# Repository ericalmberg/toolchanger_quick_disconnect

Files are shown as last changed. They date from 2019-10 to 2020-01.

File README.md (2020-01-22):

# toolchanger_quick_disconnect

## Statement of Purpose

The PCB in here is intended to be a universal connector board based around the micro-molex 3.0 connectors commonly used in 3D printing electronics. This board in it's current iteration contains 4x 2-pin micro-molex connectors for connections to
- Heater catridge 
- Thermistor
- Part cooling fan
- Hotend fan

The board also includes on 4 pin XH2.54 connector for a stepper motor connection if the tool is direct drive, as well as pinout for 4 additional connections back to the duet for the user's purpose labeled accessory 1-4. These are provided in the form of 0.1" spaced through hole connections. 

The connection back to the duet is provided through a 2-row, 16 pin micro-molex 3.0 connector. The intention is that the toolchanger tool wiring could be replaced with one 16 pin connector, and tools could easily be interchanged to "live" and offline. This still requires a tool library to be built into the duet code in order to store tool pickup location offsets, configurations, z-offsets and any other parameters that need to be changed when switching between tools. 

## Potential Gotchas
 - Watch out for your thermistor/PT100 amplifier inputs. Since these are hardwired at the duet, on the same tool bay the user cannot swap between thermistor based tools and PT100/thermocouple based tools.

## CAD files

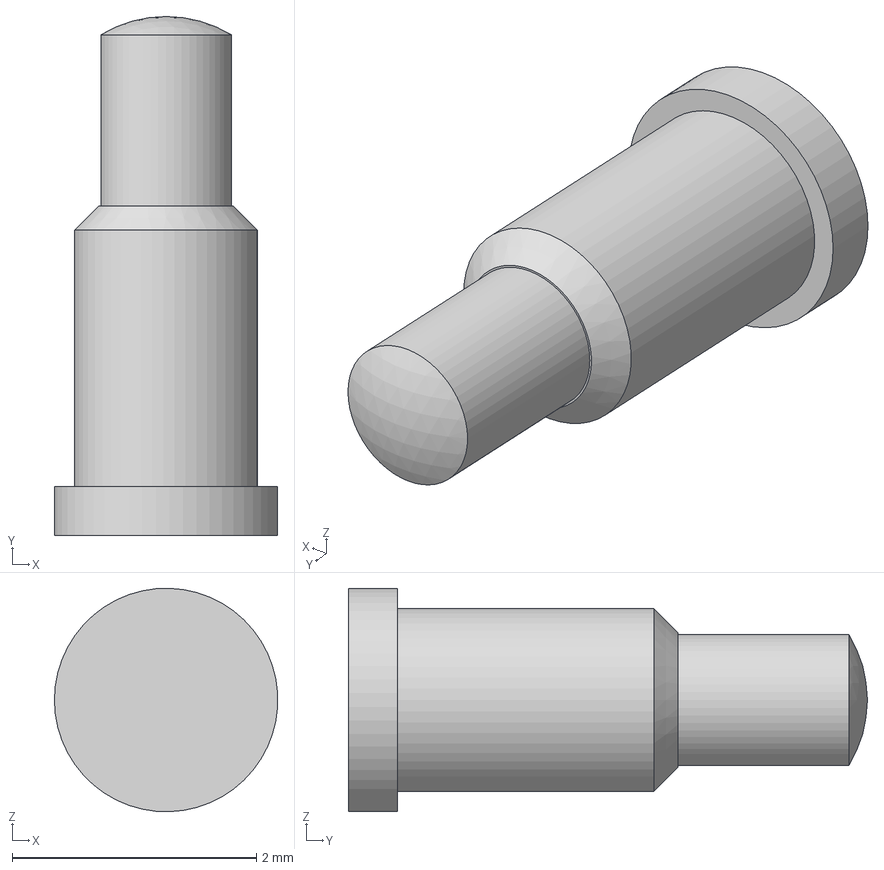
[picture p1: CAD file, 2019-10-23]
lbr/Preci-dip_90022-AS v1.step
1.83 x 4.25 x 1.83 mm

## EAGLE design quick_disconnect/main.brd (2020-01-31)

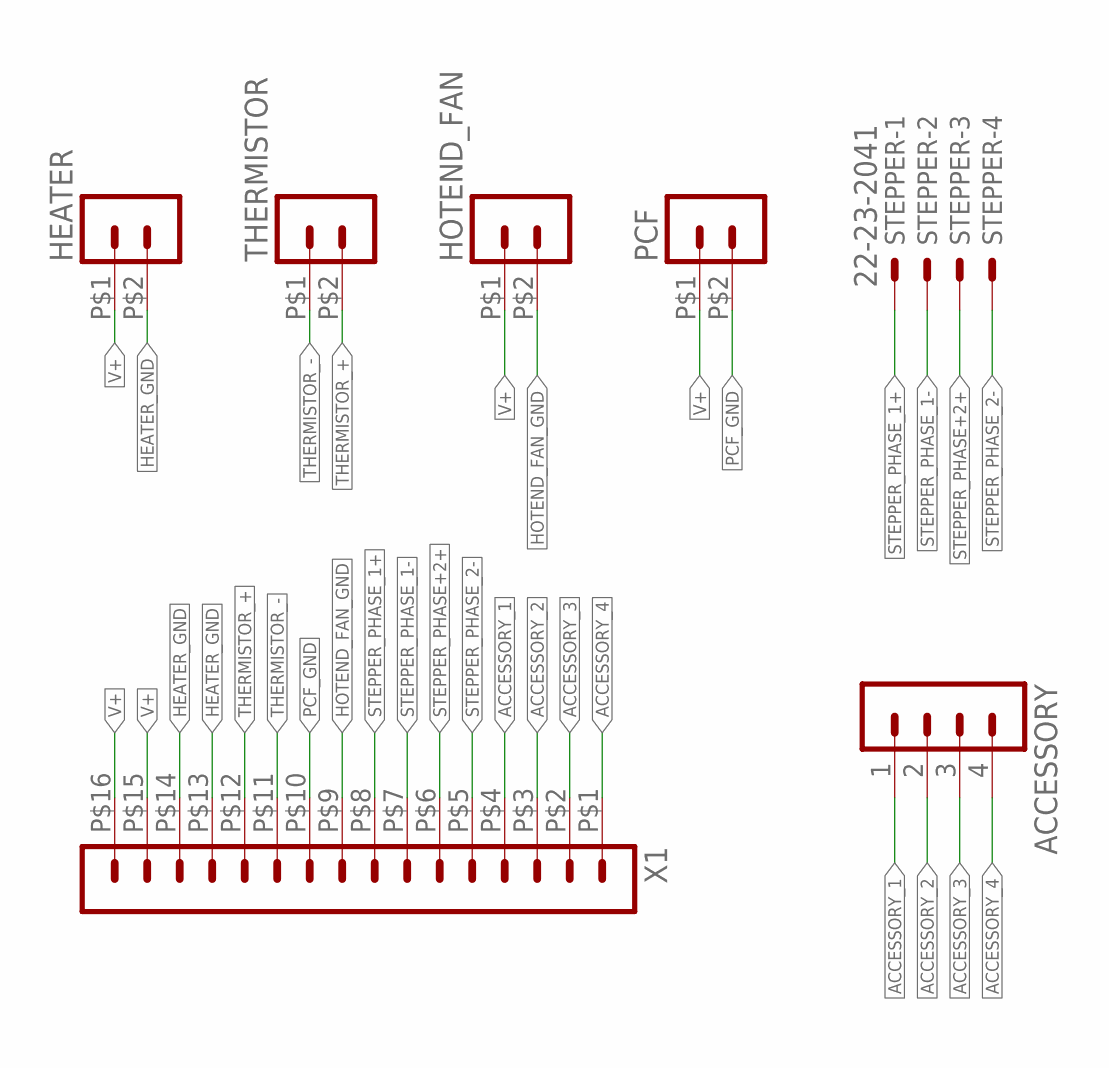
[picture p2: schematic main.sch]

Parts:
ACCESSORY: MA04-1
HEATER: HEADER_POS2_43650-0224; 43650-0224
HOTEND_FAN: HEADER_POS2_43650-0224; 43650-0224
PCF: HEADER_POS2_43650-0224; 43650-0224
STEPPER: 22-23-2041
THERMISTOR: HEADER_POS2_43650-0224; 43650-0224
X1: HEADER_POS16_43045-1618; 43045-1618

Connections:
ACCESSORY_1: ACCESSORY.1, X1.P$4 (4)
ACCESSORY_2: ACCESSORY.2, X1.P$3 (3)
ACCESSORY_3: ACCESSORY.3, X1.P$2 (2)
ACCESSORY_4: ACCESSORY.4, X1.P$1 (1)
HEATER_GND: HEATER.P$2 (2), X1.P$13 (13), X1.P$14 (14)
HOTEND_FAN_GND: HOTEND_FAN.P$2 (2), X1.P$9 (9)
PCF_GND: PCF.P$2 (2), X1.P$10 (10)
STEPPER_PHASE+2+: STEPPER.3, X1.P$6 (6)
STEPPER_PHASE_1+: STEPPER.1, X1.P$8 (8)
STEPPER_PHASE_1-: STEPPER.2, X1.P$7 (7)
STEPPER_PHASE_2-: STEPPER.4, X1.P$5 (5)
THERMISTOR_+: THERMISTOR.P$2 (2), X1.P$12 (12)
THERMISTOR_-: THERMISTOR.P$1 (1), X1.P$11 (11)
V+: HEATER.P$1 (1), HOTEND_FAN.P$1 (1), PCF.P$1 (1), X1.P$15 (15), X1.P$16 (16)

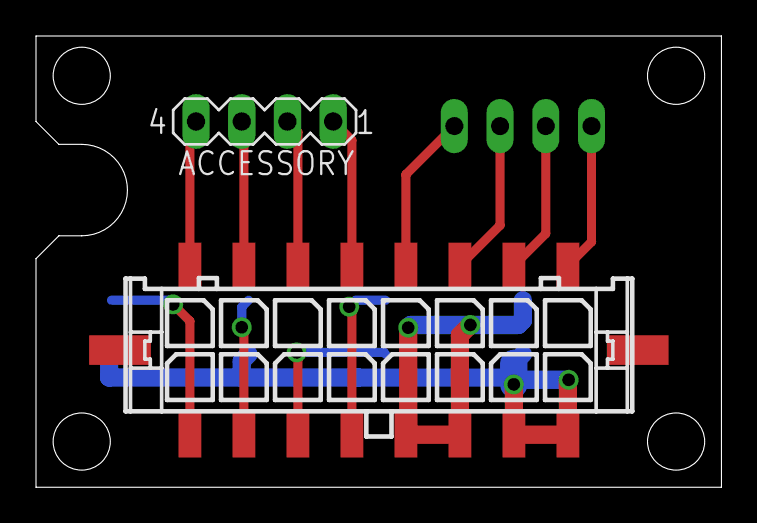
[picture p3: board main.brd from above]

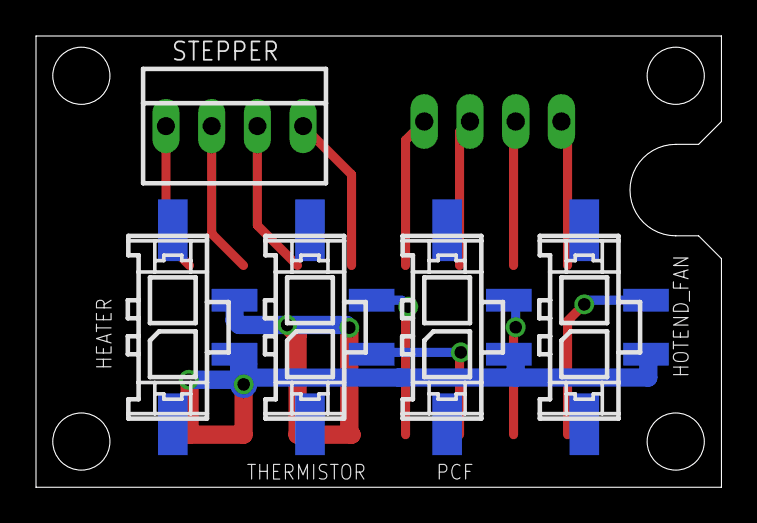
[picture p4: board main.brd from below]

Board: 2 copper layers, 38.1 x 25.1 mm, 7 parts (5 on the bottom side), 14 nets.

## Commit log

2019-10-23 first commit and schematic with only pogo pins
    [Preci-dip_90022-AS v1.step, main.brd, main.sch]
2020-01-22 initial design of 4x 2pin molex, 1x 16 pin molex, 4 header acc
    [main.brd, main.sch]
2020-01-22 small routing updates
    [main.brd]
2020-01-31 via updates to allow manual soldering, cutout on the side to allow for ptfe tube passthrough
    [main.brd, main.sch]
